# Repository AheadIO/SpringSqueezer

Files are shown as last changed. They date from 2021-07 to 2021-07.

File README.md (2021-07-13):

# SpringSqueezer
A cable mechanism testing machine. It uses Springs as load - that where the names comes from.

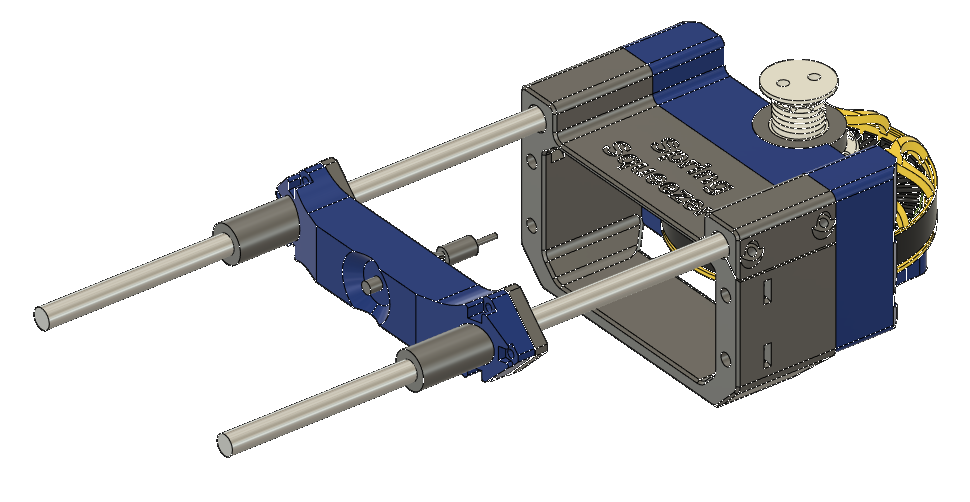
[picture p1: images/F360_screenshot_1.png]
Spring Squeezer F360 Screenshot 1


## What can be tested:
This machine allows for practical evaluation of a capstan based cable mechanism. It works only for Capstan mechanisms that fasten the cable on the small drum and relay on that as a significant part of their load-bearing capability. An example of such a mechanism is the one we use on our robot - Stanley.

Aspects that can be tested:
<ul>
<li>Friction wear on the drum and cable
<li>Fatigue damage of the  cable
<li>Reliability and durability of termination
<li>Slippage of the cable through the drum mounting points
</ul>

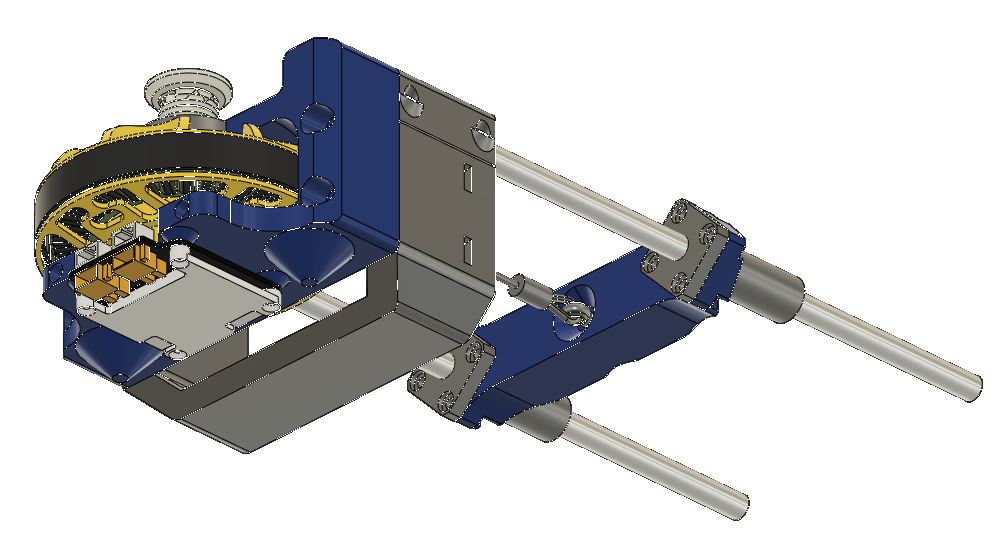
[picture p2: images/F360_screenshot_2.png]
Spring Squeezer F360 Screenshot 1


## Hardware:
### Printed:
You will need to print two major structural parts of the machine - the motor mount and the rod scaffolding and 3 smaller parts - the cable termination block and the top and bottom of the drum

### Bought:
<ul><li>
motor - Eaglepower 8308 https://pl.aliexpress.com/item/4000563826414.html?spm=a2g0s.9042311.0.0.27425c0fCLdyW7
<li> driver - moteus r4.5 (compatible with r4.3)
https://mjbots.com/collections/servos-and-controllers/products/moteus-r4-5
<li> mjbots CANFD to USB adapter - https://mjbots.com/collections/accessories/products/fdcanusb
<li> PSU capable of ~500W at 24-34V
<li>2x clamps to clamp ot to the desk
<li>4x M2.5x10 screws for the moteus driver (if no heatsink) or 4x M2.5x16 countersunk screws for the moteus driver (if org moteus heasink used)
<li>4x M4x12 hex screws- to screw down the Eaglepower 8308
<li>4x M5x50 hex screws - for connecting the linear_rod_holder with the motor_cage
<li>4x M5 square nuts - for connecting the linear_rod_holder with the motor_cage
<li>2x M4x30  hex screws - for the capstan drum
<li>2x M4 square nuts - for the capstan drum
<li>6x M3x10 countersunk hex screws - 4 of them for mounting capstan drum to the motor and 2 of the act as drum reinforcement (they screw from the bottom of "capstan_mech_small_drum_bottom")<li>4x M3x20 hex screws - for tightening the 8mm linear rod mounts
<li>6x M3x15 hex screws - for mounting the LMK8LUU linear bearings
<li>2x M3x50 hex screws - they act as structural reinforcement of the motor cage
<li>12x M3 square nuts - 4 of them for tightening the 8mm linear rod mounts, 6 of them for mounting the LMK8LUU linear bearings and 2 of them for the long structural reinforcement screws
<li>1x M5 eye bolt - or you can adapt to any other mounting method you want to use in your robot. M5 eye bolt we use: https://pl.aliexpress.com/item/1005001623167300.html?spm=a2g0s.9042311.0.0.37aa5c0fBCzdPX 
<li>1x M5 nut - for the M5 eye bolt
<li>1x Cable assembly (ours includes a crimp and 1.5mm DYNEEMA rope, but it ommits the thimble, yours can be different)
<li>2x LMK8LUU linear bearings
<li>2x 250~300mm linera rods
<li>2x Springs - We used 1,5x12x75 - but feel free to experiment with outer lengths/stifnesses - just make sure that the internal dimeter is bigger than 8

</ul>

## Software

Included in this repo in the software folder is a screipt that automates the testing. You set the parameters to your liking. You need to make sure that the system is thermaly stable and you don't cook your motor. We highly recommend pointing some kind of fan at the assembly during the tests. The deafults are what we used for our testing. The vairables with description:
<ul>
<li>pull_duration - first part of the cycle - over this amount of time the motor pulls the cable with full Troque
<li>release_duration next part of the cycle - a gradual release starting at max torque ending at standby_torque
<li>duty_cycle - cycle of the test
<li>max_torque - maximum torque exerted by the motor
<li>standbay_torque - between pulls the motor still exerts some torque - to keep the cable tight
<li>rotational_speed_safety_limit - if motor spins above that rotational velocity the test is interrupted - this makes sure that the test does not continue after the rope breaks
</ul>

## Usage

Fasten the rig to your cable with clamps, assemble your rope, set the parameters, point the fan at the test rig, make sure the rig is thermally stable and run the test till something breaks. If you interrupt the test, and you want to start it again but you want the count to continue- not start from zero - you should set the previous amount as the value of the "counter" variable.

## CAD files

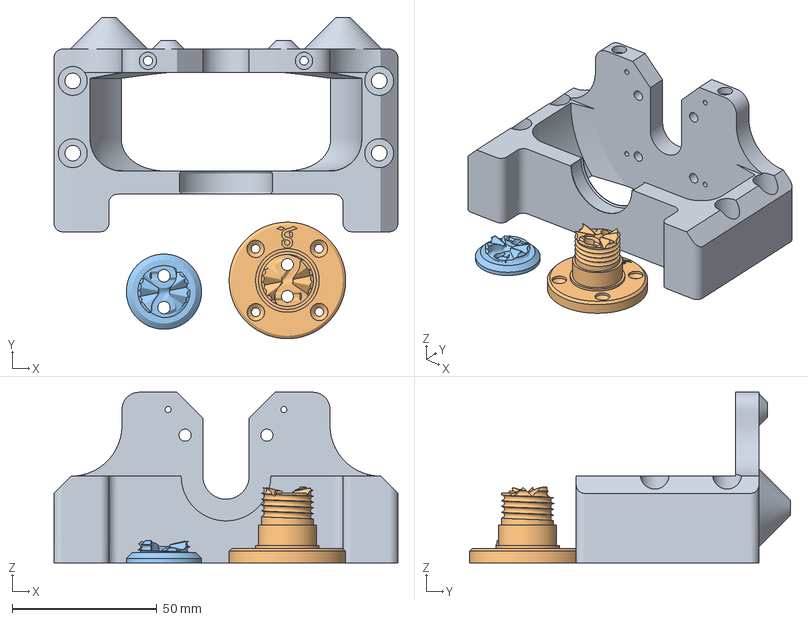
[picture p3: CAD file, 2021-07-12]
3D_printing/print_in_high_temp_plastic.3mf
119.0 x 111.2 x 59.0 mm
motor_cage-print_in_high_temp_plastic.stl
capstan_mech_small_drum_bottom-print_in_high temp_plastic.stl
capstan_mech_small_drum_top-print_in_high_temp_plastic.stl

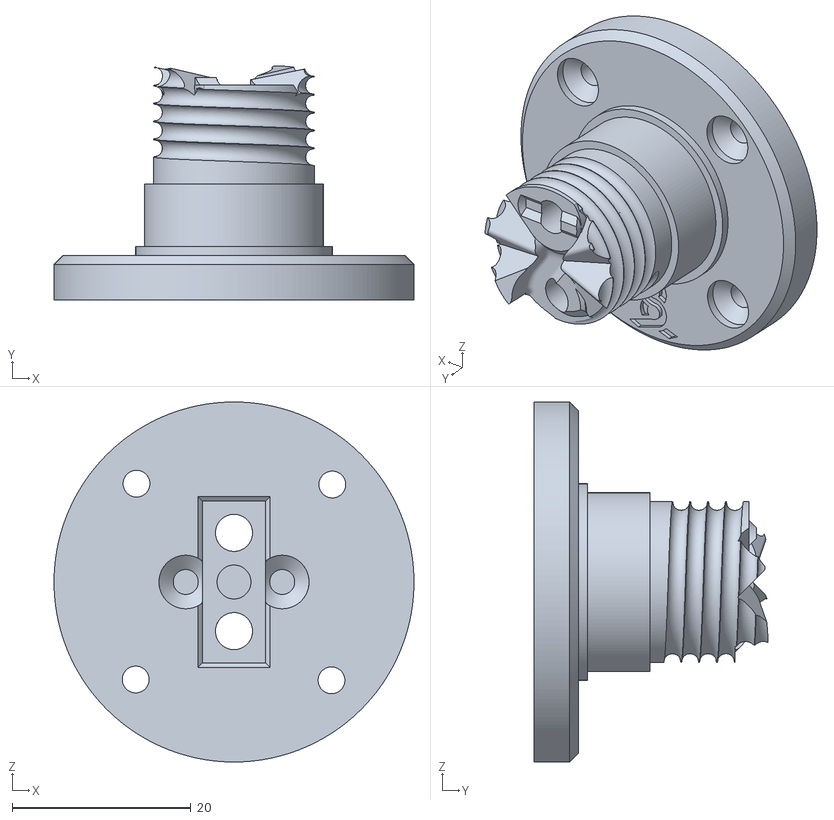
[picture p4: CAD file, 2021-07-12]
3D_printing/capstan_mech_small_drum_bottom-print_in_high temp_plastic.stl
40.3 x 26.2 x 40.3

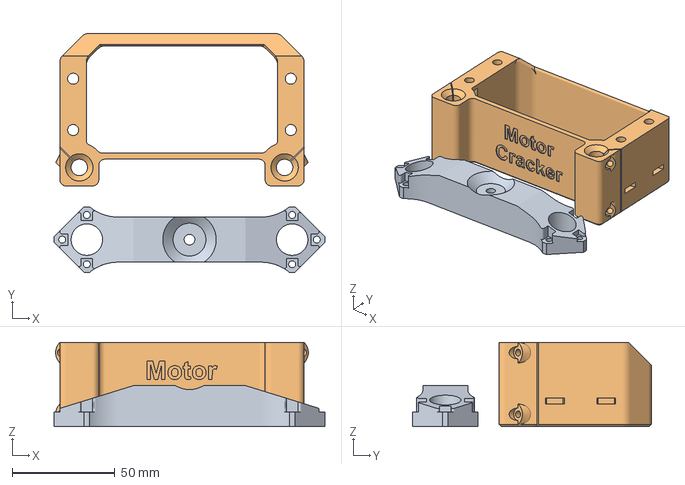
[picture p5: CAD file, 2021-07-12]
3D_printing/print_in_any_plastic.3mf
132.0 x 116.4 x 41.0 mm
cable_termination_block-print_in_any_plastic.stl
linear_rod_holder-print_in_any_plastic.stl

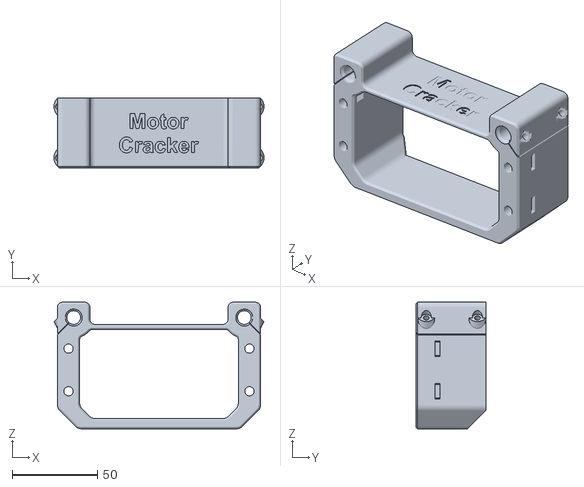
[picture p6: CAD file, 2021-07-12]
3D_printing/linear_rod_holder-print_in_any_plastic.stl
123.1 x 41.0 x 74.2

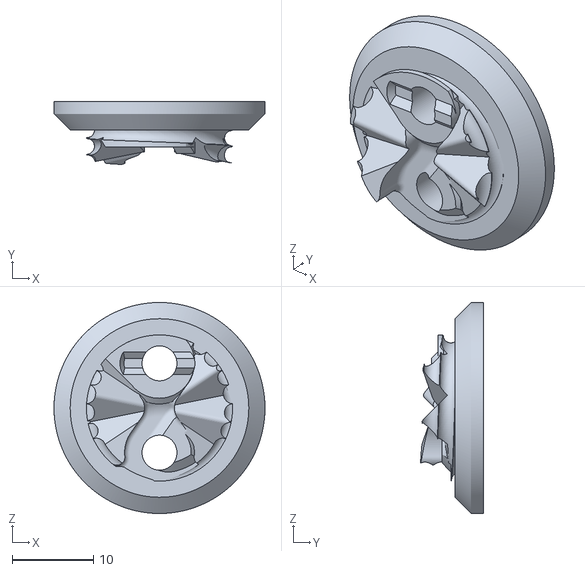
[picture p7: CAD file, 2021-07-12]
3D_printing/capstan_mech_small_drum_top-print_in_high_temp_plastic.stl
26.0 x 7.73 x 26.0

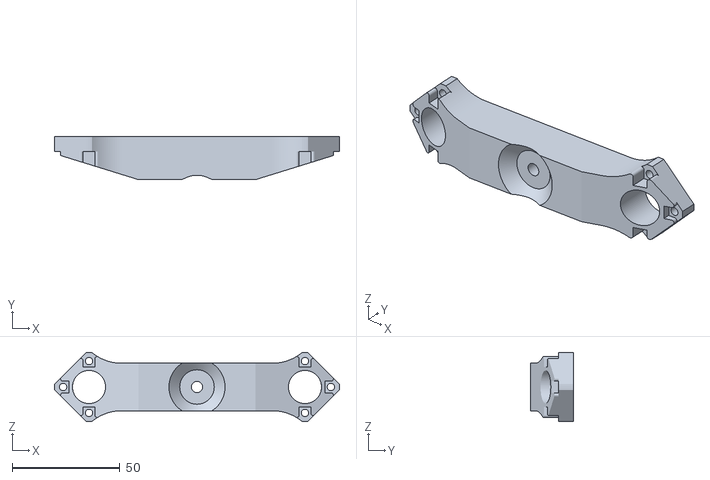
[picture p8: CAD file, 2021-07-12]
3D_printing/cable_termination_block-print_in_any_plastic.stl
132.0 x 20.0 x 32.0

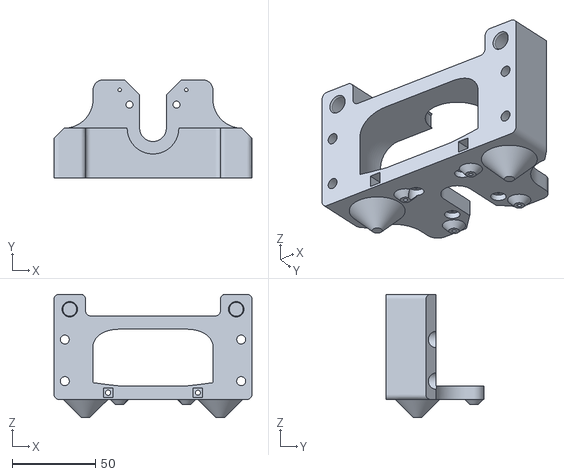
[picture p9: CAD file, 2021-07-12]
3D_printing/motor_cage-print_in_high_temp_plastic.stl
119.0 x 59.0 x 74.2

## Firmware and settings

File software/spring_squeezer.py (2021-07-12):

from moteus_fdcan_adapter import Controller
from moteus_fdcan_adapter import MoteusReg
import time

def main():
    #############################################   SETUP PARAMETERS   ################################################
    pull_duration = 0.1 # First part of the cycle - over this amount of time the motor pulls the cable with full Troque
    release_duration = 0.1 # next part of the cycle - a gradual release starting at max torque ending at standby_torque
    duty_cycle = 1 #duty cycle of the test
    max_torque = 3 #maximum torque exerted by the motor
    standbay_torque = 0.1 #between pulls the motor still exerts some torque - to keep the cable tight
    rotational_speed_safety_limit = 25 #if motor spins above that rotational vel the test is interrupted - this makes sure that the test does not continue after the rope breaks
    counter = 0 #if you had to interrupt testing and need to start again but not count from 0 - input the number starting number you want here
    ###################################################################################################################

    c = Controller(controller_ID=1) #create controller object
    c.command_stop() #comand_stop cleares anny errors/faults in the controller
    max_measured_velocity = 0 #this variable stores the max measured rotational velocity of the motor and is used for safety and can be observed as an erformance indicator
    time_zero = time.time()
    previous_phase = 0 #variable used to detect switching from one cycle to the next
    while True:
        phase = (time.time()-time_zero) % (duty_cycle) #what is happening during the cycle depends on the phase value. Phase is in seconds

        #below - the behaviour of the system is dependent on the value of phase - in different value ranges different behaviours are triggered
        if phase < pull_duration:
            #initiall full torque pull
            measurements = c.set_position(position = 0, max_torque=4, ff_torque=max_torque, kp_scale=0, kd_scale=0,
                                          get_data=True, print_data=False) #measurements are collected to extract velocity - which if too high stops the system (safety)
        elif phase >= pull_duration and phase <= pull_duration+release_duration:
            #gradual release
            release_phase = ((pull_duration+release_duration-phase)/release_duration) #value normalized from 1 to 0.
            torque = standbay_torque+(max_torque-standbay_torque)*release_phase #torque ges from max_torque to standby_torque
            measurements = c.set_position(position = 0, max_torque=4, ff_torque=torque, kp_scale=0, kd_scale=0,
                                          get_data=True, print_data=False) #measurements are collected to extract velocity - which if too high stops the system (safety)
        else:
            measurements = c.set_position(position = 0, max_torque=4, ff_torque=standbay_torque , kp_scale=0,
                                          kd_scale=0.1, get_data=True, print_data=False) #measurements are collected to extract velocity - which if too high stops the system (safety)

        if max_measured_velocity < abs(measurements[MoteusReg.MOTEUS_REG_VELOCITY]): #for diagnostics
            max_measured_velocity = abs(measurements[MoteusReg.MOTEUS_REG_VELOCITY])
            print("Max velocity that occured so far: " + str(abs(measurements[MoteusReg.MOTEUS_REG_VELOCITY])))
        if max_measured_velocity>rotational_speed_safety_limit: break

        if (previous_phase > phase): #code for counting phase cycles
            counter = counter + 1
            print("Temperature = " + str(measurements[MoteusReg.MOTEUS_REG_TEMP_C]) + "  Counter = " + str(counter))
        previous_phase = phase


    c.set_position(position=0, velocity=0, max_torque=1, ff_torque=0, kp_scale=0, kd_scale=1,
                   get_data=True, print_data=False) #if there is a break in the loop above - the velocity limit is exceeded - this command stops the rotr

if __name__ == '__main__':
    main()

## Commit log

2021-07-12 added software for spring squeezer
2021-07-12 added printing and design files
    [cable_termination_block.stl, capstan_mech_small_drum_bottom.stl, capstan_mech_small_drum_top.stl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]
2021-07-12 updated small drum designs
    [capstan_mech_small_drum_bottom.stl, capstan_mech_small_drum_top.stl]
2021-07-12 printing files updated
    [cable_termination_block-print_in_any_plastic.stl, cable_termination_block.stl, capstan_mech_small_drum_bottom-print_in_high temp_plastic.stl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]
2021-07-12 readme and BOM written, small updates to design and printing files
    [capstan_mech_small_drum_bottom-print_in_high temp_plastic.stl, print_in_high_temp_plastic.3mf]
2021-07-13 PSU and CANFD adapter added to the BOM
2021-07-13 forgot about springs!
